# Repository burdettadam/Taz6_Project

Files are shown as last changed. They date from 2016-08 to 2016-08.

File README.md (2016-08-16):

# Taz6_Project
Analysis of building a cheap clone of the taz6 3d printer. 
# Goal
our goal is to analyse LulzBot TAZ 6 (https://www.lulzbot.com/store/printers/lulzbot-taz-6) open source 3d printer to create a cheap clone build by looking at alternative hardware and resulting trade offs.
all source files where taken from http://download.lulzbot.com/TAZ/6.0/. another place for source files can be found at http://devel.lulzbot.com/TAZ/Olive/
#to do
    -collect taz 6 source files-done
    -structure source files-done
    -created parts list with price total
#BOM
| Category | Part | Quantity |seller | Price |
|---|:---:|---:|---:|---:|
| Printed  |[Y Motor Mount v3.0](https://github.com/burdettadam/Taz6_Project/blob/master/production_parts/printed_parts/y_motor_mount/y_motor_mount_v3.0.stl),TAZ | 1 | | |
| |[Y mount table v~~2.5~~3.1](https://github.com/burdettadam/Taz6_Project/blob/master/production_parts/printed_parts/bed_mount_table/bed_mount_table_v3.1.stl), TAZ | 4 | | |
| |[Y Mount Chassis v~~2.5~~3.3A](https://github.com/burdettadam/Taz6_Project/blob/master/production_parts/printed_parts/bed_mount_chassis/bed_mount_chassis_v3.3_A.stl), TAZ | 4 | | |
| |[y idler mount v4.0](https://github.com/burdettadam/Taz6_Project/blob/master/production_parts/printed_parts/y_idler_mount/y_idler_mount_v4.0.stl), TAZ | 4 | | |
| |[Y belt mount v2.5](https://github.com/burdettadam/Taz6_Project/blob/master/production_parts/printed_parts/y_belt_mount/y_belt_mount_v0.75-x2.stl), TAZ | 1 | | |
| |[y corner left v2.4](https://github.com/burdettadam/Taz6_Project/blob/master/production_parts/printed_parts/y_corner_left/y_corner_left_v2.4.stl), TAZ | 4 | | |
| |[y corner right v2.4](https://github.com/burdettadam/Taz6_Project/blob/master/production_parts/printed_parts/y_corner_right/y_corner_right_v2.4.stl), TAZ | 4 | | |
| |[Bed corner ninjaflex-? v2.0](https://github.com/burdettadam/Taz6_Project/blob/master/production_parts/printed_parts/bed_corner_taz6/bed_corner_taz6_v2.stl), TAZ |  4 | | |
| |[bearing holder v1.0](https://github.com/burdettadam/Taz6_Project/blob/master/production_parts/printed_parts/bearing_holder/bearing_holder_v1.0.stl), TAZ |  ? | | |
| |[zmin switch mount v4.1](https://github.com/burdettadam/Taz6_Project/blob/master/production_parts/printed_parts/zmin_switch_mount/zmin_switch_mount_v4.1.stl) | 1 | | |
| |[Z-lower left](https://github.com/burdettadam/Taz6_Project/blob/master/production_parts/printed_parts/z_lower_left/z_lower_left_v2.5.stl) v2.5  | 2 | | |
| |[Z-lower right](https://github.com/burdettadam/Taz6_Project/blob/master/production_parts/printed_parts/z_lower_right/z_lower_right_v2.5.stl) v2.5  | 2 | | |
| |[Z Carriage Idler](https://github.com/burdettadam/Taz6_Project/blob/master/production_parts/printed_parts/z_carriage_idler/z_carriage_idler_v2.9.1.stl) | 1 | | |
| |[Z Carriage Motor](https://github.com/burdettadam/Taz6_Project/blob/master/production_parts/printed_parts/z_carriage_motor/z_carriage_motor_v2.10.stl) | 1 | | |
| |[Fan duct right v0.1](https://github.com/burdettadam/Taz6_Project/blob/master/production_parts/printed_parts/fan_duct_right/fan_duct_right_v0.7.4.1d.stl), TAZ |1 | | |
| |[Fan duct left v0.1](https://github.com/burdettadam/Taz6_Project/blob/master/production_parts/printed_parts/fan_duct_left/fan_duct_left_v0.7.4.1d.stl), TAZ |  1 | | |
| |[Single Bearing Holder for 12mm rod](https://github.com/burdettadam/Taz6_Project/blob/master/production_parts/printed_parts/12mm_single_bearing_holder/12mm_single_bearing_holder_v0.4.stl) v0.3 | 1 | | |
| |[Double Bearing Holder for 12mm rod](https://github.com/burdettadam/Taz6_Project/blob/master/production_parts/printed_parts/12mm_double_bearing_holder/12mm_double_bearing_holder_v0.7.stl) v0.3 | 1 | | |
| |[X-Carriage Guide](https://github.com/burdettadam/Taz6_Project/blob/master/production_parts/printed_parts/x_carriage_guide/x_carriage_guide_v2.stl) v2.0, TAZ | 1 | | |
| |[X-Carriage](https://github.com/burdettadam/Taz6_Project/blob/master/production_parts/printed_parts/x_carriage_taz6/x_carriage_taz6_v0.3.stl) v2.0, TAZ |1 | | |
| |[Wade extruder body for Hex nozzle](https://github.com/burdettadam/Taz6_Project/blob/master/production_parts/printed_parts/extruder_body_hex/extruder_body_hex_v1.4.1.stl) v1.0 |1 | | |
| |[Wiper mount](https://github.com/burdettadam/Taz6_Project/blob/master/production_parts/printed_parts/wiper_mount/wiper_mount_v1.1.stl) v2.0 |1 | | |
| |[extruder_latch_v2.1](https://github.com/burdettadam/Taz6_Project/blob/master/production_parts/printed_parts/extruder_latch/extruder_latch_v2.1.stl) | 1 | | |
| |[herringbone_small_gear](https://github.com/burdettadam/Taz6_Project/blob/master/production_parts/printed_parts/herringbone_small_gear/herringbone_small_gear-1.1-highres.stl) | 1 | | |
| |[herringbone_large_gear](https://github.com/burdettadam/Taz6_Project/blob/master/production_parts/printed_parts/herringbone_large_gear/herringbone_large_gear_v1.3.stl) | 1 | | |
| |[Wade Reloaded Bearing Washer](https://github.com/burdettadam/Taz6_Project/blob/master/production_parts/printed_parts/extruder_washer/extruder_washer_v3.0-x16.stl) | 1 | | |
| |[extruder_mount -?](https://github.com/burdettadam/Taz6_Project/blob/master/production_parts/printed_parts/extruder_mount_taz6/extruder_mount_taz6_v0.8.stl) | 1 | | |
| |[Wade Reloaded Idler Block](https://github.com/burdettadam/Taz6_Project/blob/master/production_parts/printed_parts/extruder_idler_block/extruder_idler_block_v1.4c.stl) v1.4, Taz | 1 | | |
| |[Feed Tube Spinner v2.5](https://github.com/burdettadam/Taz6_Project/blob/master/production_parts/printed_parts/feed_tube_spinner/feed_tube_spinner_v3.0.stl) | 1 | | |
| |~~Feed Tube Holder v2.5~~ -?  | 1 | | |
| |[tippy_feed_tube_holder_v0.6](https://github.com/burdettadam/Taz6_Project/blob/master/production_parts/printed_parts/tippy_feed_tube_holder/tippy_feed_tube_holder_v0.6.stl) -?damage stl?  | 1 | | |
| |[Spool Arm v2.0](https://github.com/burdettadam/Taz6_Project/blob/master/production_parts/printed_parts/spool_arm/spool_arm_v0.2-x2.stl), TAZ | 1 | | |
| |[heatsink fan duct](https://github.com/burdettadam/Taz6_Project/blob/master/production_parts/printed_parts/heatsink_fan/heatsink_fan_duct_v0.6.stl) | 1 | | |
| |[Z-Upper](https://github.com/burdettadam/Taz6_Project/blob/master/production_parts/printed_parts/z_upper/z_upper_v2.4.stl) v2.4 |  1 | | |
| |[LCD Bezel v1.1](https://github.com/burdettadam/Taz6_Project/blob/master/production_parts/printed_parts/lcd_bezel/lcd_bezel_v1.1.stl) |  4 | | |
| |[LCD Knob 0.2 design dent 2](https://github.com/burdettadam/Taz6_Project/blob/master/production_parts/printed_parts/lcd_knob/lcd_knob_0.2_design_dent_2.stl) |  1 | | |
| |[LCD spacer](https://github.com/burdettadam/Taz6_Project/blob/master/production_parts/printed_parts/lcd_spacer/lcd_spacer_v0.4.stl) |  4 | | |
| |[Sd Card Bezel v0.8](https://github.com/burdettadam/Taz6_Project/blob/master/production_parts/printed_parts/sd_card_bezel/sd_card_bezel_v0.8-x10.stl) |  4 | | |
| |[Electronics Case Mount v1.0](https://github.com/burdettadam/Taz6_Project/blob/master/production_parts/printed_parts/electronics_case_mount/electronics_case_mount_v2.0.stl) | 4 | | |
| |[Interconnect housing v0.1](https://github.com/burdettadam/Taz6_Project/blob/master/production_parts/printed_parts/interconnect_housing/interconnect_housing_v0.6.stl), TAZ |  1 | | |
| |[flexy washer v0.1](https://github.com/burdettadam/Taz6_Project/blob/master/production_parts/printed_parts/flexy_washer/flexy_washer_v0.1.stl), TAZ |  1 | | |
| |[flexy bed foot v0.1](https://github.com/burdettadam/Taz6_Project/blob/master/production_parts/printed_parts/flexy_bed_foot/flexy_bed_foot_v0.1.stl), TAZ |  1 | | |
| | | | | |
| Electronic | | | | |
| | | | | |
| Hardware | | | |
| | | | | |
| | | | [aliexpress](http://www.aliexpress.com/item/5-Hole-90-Degree-Joint-Board-Plate-Corner-Angle-Bracket-Connection-Joint-Strip-for-Aluminum-Profile/32669228356.html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,searchweb201602_1_10057_10056_10055_10049_10059_10058_10017_106_105_104_10060_103_10061_102_10062_10064,searchweb201603_1&btsid=93fedafa-1d70-452a-961e-7a9f04ef4315) | |
| Software | | | | |

#hardware lis cut paste from assemble instructions 
##Frame Sub Assy
4x- 500mm Aluminum Extrusion, M5 threaded one end  
4x- 510mm Aluminum Extrusion, ends not threaded  
41x- M5 T-Nut  
32x- M5x10 BHCS  
32x- M5 Washer, Black  
8x- Corner gussets  

##Bed Assy Sub
1x- Z switch mount (PP-GP0216)  
1x- Wiper Mount (PP-GP0231) and Wiper pad  
4x- Bearings Holder (PP-GP0233) (with bearings installed)  
4x- Bed corners (PP-GP0221)  
1x- Y belt mount (PP-GP0222)  
1x- Bed plate  
4x- Bed standoffs  
1x- Momentary switch and retention nut  
2x- SPDT switches  
1x- M3x16 FHCS  
30x- M3x8 BHCS  
4x- M2x10 SHCS  
1x- M3x10  
30x- M3 black washers  
4x- M2 washers  

##Y Axis Sub_Edit
16x- M5x10 BHCS  
16x- M5 Black Washer  
1x- M8x35 BHCS  
4x- M8 Washers  
2x- 608 bearings  
4x- M3x12 BHCS  
4x- M3 Black washers  
4x- M3x6 Set screws  
2x- 500mm aluminum extrusions  
16x- M5 T-Nut  
8x- M5x10 BHCS  

##Y axis end plate- Motor side
4x- M3x 10 BHCS  
4x- M3 Black Washer  
1x- Taz 6 Y Motor Mount (PP-GP0226)  
with 4x- M3 inserts installed  
1x- Y axis End plate  

##Idler assembly
1x- Idler mount (PP-GP0225) (with 4x M3 inserts)  
1x- M8 x40 BHCS  
4x- M8 Washer  
1x- M8 Nyloc Nut  
2x- 608 Bearing  

##Y Axis Idler end plate Assembly
4x- M3x 10 BHCS  
4x- M3 Black Washer  
1x- Taz 6 Y Axis Idler Assembly  
1x- Y axis End plate

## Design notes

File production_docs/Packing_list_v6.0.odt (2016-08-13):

Model: LulzBot TAZ 6 3D Printer

Serial Number: _______________________

Date Completed: _______________________

Completed by: _______________________

Items to include:

Printer and Cables:

- LulzBot TAZ 6 3D printer
- 1.83 meter (6ft) 18AWG North America Power Cord Cable
- 1.83 meter (6ft) 18AWG United Kingdom Power Cord Cable (If applicable)
- 1.83 meter (6ft) 18AWG Europe Power Cord Cable (If applicable)
- 1.83 meter (6ft) 18AWG Australia Power Cord Cable (If applicable)
- USB cord
- Filament guide tube with mounting clip
- Tool head assembly

Supplies:

- SD Card with source files
- Tool kit
- Sample material
- LulzBot sticker

Documentation:

- Unboxing guide
- Operating guide
- Test acceptance record
- Packing list
- User manual
- EC Declaration of Conformity
- Safety and warning sheet
- Modification warning

Final Print:

- Octopus printed by this LulzBot TAZ 3D Printer. Octopus_v18 by yeoldbrian is licensed under CC BY-SA 4.0

Packing List

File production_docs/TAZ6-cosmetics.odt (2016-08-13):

Purpose and Scope:

The purpose of this standard is to provide cosmetic requirements for printed components on TAZ 6. See 'Cosmetic Specification Requirements' document for definitions not included in this document. This does not include specifications for secondary operations such as inserts.

Components:

Z Upper

Z Lower

Z Carriage Idler

Z Carriage Motor

Z Gaskets

LCD Bezel:

Surface A as indicated should be free of any defects. All other surfaces not noted are defined as a 'D' surface.

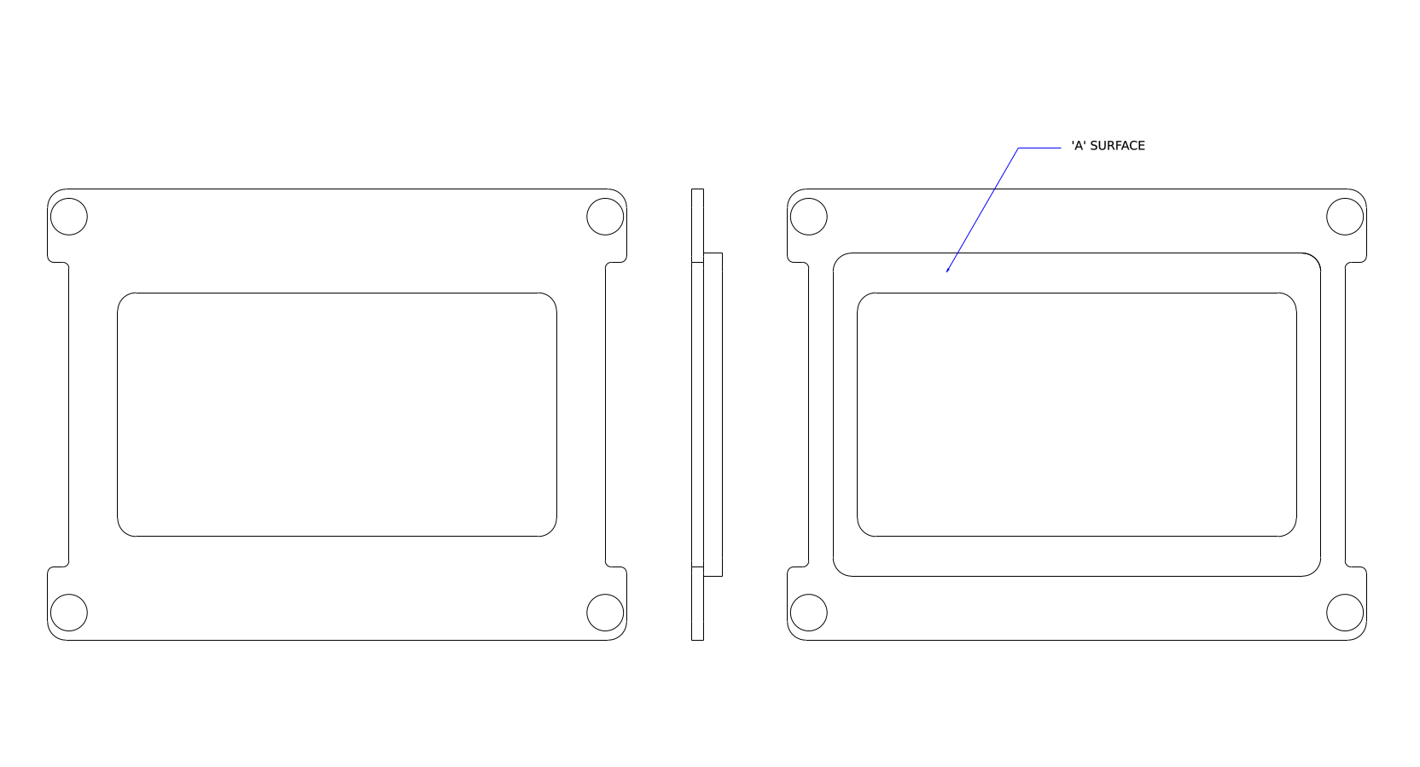
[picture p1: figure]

LCD Knob

SD Card

Lift: Lifting along an edge with a visible ridge.

(need sample picture)

Over squish: A solid first layer is present, the outside perimeter tapers out.

(need sample picture)

Resonance: See Ringing

(need sample picture)

Ringing: Wavy pattern after side face cutouts/holes.

(need sample picture)

Warp: Curling of the print at stressed locations of the print.

(need sample picture)

Wrinkling: Waving in the perimeter wall

(need sample picture)

II. Surface identifications and Classification of Surface Finish

“A” Surface – The top or front, most often viewed surface

“B” Surface – Generally the front edge and sides of a part. Not Viewed as often as an “A” surface but easily seen by user.

“C” Surface – Most often the back and bottom surface

“D” Surface - Internal surfaces. Normally D surfaces are not inspected for cosmetic attributes. Where necessary, D surfaces will be specified as an exception.

III. Standard Viewing Condition

A. Lighting Intensity

All quality decisions of cosmetic acceptability will be made under normal lighting conditions (80-120 footcandles) in white fluorescent light.

B. Viewing Angle

All viewing will take place with direct overhead lighting. Viewing angle is dependent on surface classification.

In every case, parts will be held such that the light is NOT REFLECTED directly to the viewer.

“A” Surface – Hold part 30º from the horizontal plane. Part is in direct line with your eyes.

ROTATE part 30º to the right and to the left about the vertical axis.

“B” Surface – Hold part 90º from the horizontal plane. Part is in direct line with your eyes. DO NOT rotate the part.

“C” Surface – Hold part 90º from the horizontal plane. Part is NOT in direct line with your eyes. Part is held 45º below the plane of your eyes. DO NOT rotate the part.

C. Viewing Distance

“A” Surface – 18 Inches

“B” Surface – 24 Inches

“C” Surface – 30 Inches

D. Inspection Interval (time)

Inspection interval is a function of surface area

SURFACE AREA | “A” Surfaces | Non - “A” Surfaces
≤ 4 in² ( | 2 sec | 1 sec
4-16 in² | 4 sec | 2 sec
16-64 in² | 6 sec | 3 sec
64-144 in² | 8 sec | 4 sec
> 144 in² | 10 sec | 5 sec

Cosmetic Specification Requirements TAZ 6

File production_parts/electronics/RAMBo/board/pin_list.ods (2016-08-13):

Port | Arduino Digital # | Function | RAMBo Function | Color | Function
PE0 | 0 | USART0_RX | USB/Serial Ext 3 |  | Serial
PE1 | 1 | USART0_TX | USB/Serial Ext 4 |  | MOSFET
PE4 | 2 | PWM2 | Fan-2 |  | Stepper
PE5 | 3 | PWM3 | Bed-Heat |  | I2C
PG5 | 4 | PWM4 | PS-On/PWM Ext 6 |  | Ext2
PE3 | 5 | PWM5 | PWM Ext 5 |  | Analog In
PH3 | 6 | PWM6 | Fan-1 |  | SPI
PH4 | 7 | PWM7 | Heat-1 |  | PWM
PH5 | 8 | PWM8 | Fan-0 |  | Stepper Ext
PH6 | 9 | PWM9 | Heat-0 |  | Endstop
PB4 | 10 | PWM10 | Z-Min |  | Endstop/Stepper Ext
PB5 | 11 | PWM11 | Y-Min
PB6 | 12 | PWM12 | X-Min
PB7 | 13 | PWM13 | LED/PWM Ext 3
PJ1 | 14 | USART3_TX | Serial Ext 10
PJ0 | 15 | USART3_RX | Serial Ext 9
PH1 | 16 | USART2_TX | Serial Ext 8
PH0 | 17 | USART2_RX | Serial Ext 7
PD3 | 18 | USART1_TX | Serial Ext 6
PD2 | 19 | USART1_RX | Serial Ext 5
PD1 | 20 | I2C_SDA | I2C Ext 3
PD0 | 21 | I2C_SCL | I2C Ext 4
PA0 | 22 | D22 | MX1-3
PA1 | 23 | D23 | Y-Max/MX3-3
PA2 | 24 | D24 | X-Max/MX2-3
PA3 | 25 | D25 | E1-En
PA4 | 26 | D26 | E0-En
PA5 | 27 | D27 | Z-En
PA6 | 28 | D28 | Y-En
PA7 | 29 | D29 | X-En
PC7 | 30 | D30 | Z-Max/MX2-4
PC6 | 31 | D31 | MX3-4
PC5 | 32 | D32 | MX1-4
PC4 | 33 | D33 | E1-Step
PC3 | 34 | D34 | E0-Step
PC2 | 35 | D35 | Z-Step
PC1 | 36 | D36 | Y-Step
PC0 | 37 | D37 | X-Step
PD7 | 38 | D38 | DigiPot-SS
PG2 | 39 | D39 | Y-MS2
PG1 | 40 | D40 | X-MS1
PG0 | 41 | D41 | X-MS2
PL7 | 42 | D42 | E1-Dir
PL6 | 43 | D43 | E0-Dir
PL5 | 44 | D44 | MX1-5
PL4 | 45 | D45 | MX3-5
PL3 | 46 | D46 | MX2-5
PL2 | 47 | D47 | Z-Dir
PL1 | 48 | D48 | X-Dir
PL0 | 49 | D49 | Y-Dir
PB3 | 50 | SPI_MISO | SPI Ext 3
PB2 | 51 | SPI_MOSI | SPI Ext 4
PB1 | 52 | SPI_SCK | SPI Ext 5
PB0 | 53 | SPI_SS | SPI Ext 6
PF0 | 54 | A0 | T0
PF1 | 55 | A1 | T1
PF2 | 56 | A2 | T2
PF3 | 57 | A3 | Analog Ext 8
PF4 | 58 | A4 | Analog Ext 6
PF5 | 59 | A5 | Analog Ext 4
PF6 | 60 | A6 | Analog Ext 3
PF7 | 61 | A7 | T3/Analog Ext 5
PK0 | 62 | A8 | Analog Ext 7
PK1 | 63 | A9 | E1-MS1
PK2 | 64 | A10 | E1-MS2
PK3 | 65 | A11 | E0-MS1
PK4 | 66 | A12 | E0-MS2
PK5 | 67 | A13 | Z-MS2
PK6 | 68 | A14 | Z-MS1
PK7 | 69 | A15 | Y-MS1
PG4 | 70 | D70 | Ext2 5
PG3 | 71 | D71 | Ext2 7
PJ2 | 72 | D72 | Ext2 9
PJ3 | 73 | D73 | Ext2 11
PJ7 | 74 | D74 | Ext2 13
PJ4 | 75 | D75 | Ext2 15
PJ5 | 76 | D76 | Ext2 17
PJ6 | 77 | D77 | Ext2 19
PE2 | 78 | D78 | Ext2 20
PE6 | 79 | D79 | Ext2 18
PE7 | 80 | D80 | Ext2 16
PD4 | 81 | D81 | Ext2 14
PD5 | 82 | D82 | Ext2 12
PD6 | 83 | D83 | Ext2 10
PH2 | 84 | D84 | Ext2 8
PH7 | 85 | D85 | Ext2 6

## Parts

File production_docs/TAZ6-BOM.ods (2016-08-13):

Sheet: Olive
Category | AO Part # | Description | Manufacturer | Manufacturer Part Number | Distributor | Distributor SKU | Qty Per | UOM | Price Per Unit | Price Total | Qty to Order | PO | Date | ETA | R&D notes
OK to order |  | BOLD MEANS ORDERED FOR OLIVE ALSO |  |  |  |  |  |  |  | $958.18 | 3,050
Sheet metal out for quote | received | Kim please purchase
Printed – Approved |  | Buy now, Long lead times
Printed – Not approved |  | Order now!
Not confirmed – Don't order yet
 |  | NEW part number created
already ordered
questionable |  | Toni will handle
Printed | PP-GP0226 | Y Motor Mount v3.0, TAZ |  |  |  |  | 1 | ea | $5.17 | $5.17 | 3,050
Printed | PP-GP0225 | Y Bearing Mount v3.0, TAZ |  |  |  |  | 1 | ea | $0.97 | $0.97 | 3,050
Printed | PP-GP0224 | Y mount table v2.5, TAZ |  |  |  |  | 4 | ea | $0.73 | $2.92 | 12,200
Printed | PP-GP0223 | Y Mount Chassis v2.5, TAZ |  |  |  |  | 4 | ea | $0.73 | $2.92 | 12,200 |  |  |  | resize for M5 x 12
Printed | PP-GP0222 | Y belt mount v2.5, TAZ |  |  |  |  | 1 | ea | $2.46 | $2.46 | 3,050
Printed | PP-GP0221 | Bed corner ninjaflex v1.0, TAZ |  |  |  |  | 4 | ea | $0.29 | $1.16 | 12,200
Printed | PP-GP0216 | Switch mount |  |  |  | PP-GP0216 | 1 | pcs | $2.00 | $2.00 | 3,050
Printed | PP-GP0215 | Z-lower v0.1, Mangrove left |  |  |  | PP-GP0215 | 2 | pcs | $6.00 | $12.00 | 6,100 |  |  |  | Add 2mm material for m3
Printed | PP-GP0214 | Z Carriage Idler |  |  |  | PP-GP0214 | 1 |  | $6.00 | $6.00 | 3,050 |  |  |  | Name will likely change
Printed | PP-GP0213 | Z Carriage Motor |  |  |  | PP-GP0213 | 1 |  | $6.00 | $6.00 | 3,050 |  |  |  | Name will likely change
Printed | PP-GP0212 | Fan duct right v0.1, TAZ |  |  |  |  | 1 | pcs | $1.70 | $1.70 | 3,050
Printed | PP-GP0211 | Fan duct left v0.1, TAZ |  |  |  |  | 1 | pcs | $1.70 | $1.70 | 3,050
Printed | PP-GP0210 | Single Bearing Holder for 12mm rod v0.3 |  |  |  |  | 1 | ea | $1.17 | $1.17 | 3,050
Printed | PP-GP0209 | Double Bearing Holder for 12mm rod v0.3 |  |  |  |  | 1 | ea | $2.89 | $2.89 | 3,050
Printed | PP-GP0208 | Dual fan hextruder mount v0.5 |  |  |  |  | 1 | ea | $6.51 | $6.51 | 3,050
Printed | PP-GP0207 | X-Carriage Guidev2.0, TAZ |  |  |  |  | 1 | ea | $0.76 | $0.76 | 3,050
Printed | PP-GP0206 | X-Carriage v2.0, TAZ |  |  |  |  | 1 | ea | $6.00 | $6.00 | 3,050
Printed | PP-GP0186 | Wade extruder body for Hex nozzle v1.0 |  |  |  |  | 1 | ea | $4.01 | $4.01 | 3,050
Printed | PP-GP0231 | Wiper mount v2.0 |  |  |  |  | 1 | ea | $1.00 | $1.00 | 3,050 |  |  |  | needs to be modified so m3x8 doesnt poke through bottom of plate
Printed | PP-GP0091 | extruder_latch_v2.1 |  |  |  |  | 1 | ea | $0.26 | $0.26 | 3,050
Printed | PP-GP0062 | herringbone_small_gear |  |  |  |  | 1 | ea | $0.34 | $0.34 | 3,050
Printed | PP-GP0061 | herringbone_large_gear |  |  |  |  | 1 | ea | $2.43 | $2.43 | 3,050
Printed | PP-GP0060 | Wade Reloaded Bearing Washer |  |  |  |  | 1 | ea | $0.02 | $0.02 | 3,050
Printed | PP-GP0059 | Wade Reloaded Idler Block v1.4, Taz & Mini |  |  |  |  | 1 | ea | $0.90 | $0.90 | 3,050
Printed | PP-GP0219 | Feed Tube Spinner v2.5 |  |  |  | PP-GP0219 | 1 | ea | $0.53 | $0.53 | 3,050 |  |  |  | widen hole
Printed | PP-GP0218 | Feed Tube Holder v2.5 |  |  |  | PP-GP0218 | 1 | ea | $0.66 | $0.66 | 3,050 |  |  |  | round corners
Printed | PP-GP0217 | Spool Arm v2.0, TAZ |  |  |  | PP-GP0217 | 1 | ea | $2.01 | $2.01 | 3,050 |  |  |  | should be good to go
Printed |  | heatsink fan duct |  |  |  |  | 1 | pcs | $1.25 | $1.25 | 3,050 |  |  |  | duplicate, part number at bottom of doc
Printed |  | Z-Upper v0.1 |  |  |  |  | 2 | pcs | $5.00 | $10.00 | 6,100 |  |  |  | duplicate, part number at bottom of doc
Printed | PP-GP0089 | LCD_spacer |  |  |  |  | 4 | ea | $0.10 | $0.40 | 12,200
Printed | PP-GP0154 | Electronics Case Mount v1.0 |  |  |  |  | 4 | ea | $0.24 | $0.96 | 12,200
Printed | PP-GP0220 | Interconnect housing v0.1, TAZ |  |  |  |  | 1 | pcs | $5.00 | $5.00 | 3,050
Accessories | SH-PG0031 | Anti-Static Control Products 2X3 STATIC SHLD BAG W/ZIP TOP | Uline | S-6509 | Uline | S-6509 | 1 | ea | $0.13 | $0.13 | 3,050 | PO11679 | 01/25/16 | 02/29/16 | Received OLIVE BOM Ordered. KG
Accessories | DC-LB0007 | Label, Top of Box |  |  |  |  | 1 | ea | $0.24 | $0.24 | 3,050 |  |  |  | Pending Ben and Steven – looks like these will be printed on the box
Accessories | DC-LB0024 | Label, Bottom of Box |  |  |  |  | 1 | ea | $0.24 | $0.24 | 3,050 |  |  |  | Pending Ben and Steven – looks like these will be printed on the box
Accessories | SH-PG0069 | 3M 8898 Economy Strapping Tape - 1⁄2" x 60 yards |  |  | Uline | S-16075 | 700 | mm | $0.00 | $0.09 | 2,135,000 | PO12719 | 03/29/16 | 04/04/16 | 7005 ft = 2400 yds = 48 rolls KG Have new packaging vendor quote this out.TS
Accessories | SH-PG0072 | 3M 8898 Economy Strapping Tape - 2" x 60 yards |  |  | Uline | S-16076 | 600 | mm | $0.00 | $0.50 | 1,830,000 | PO12719 | 03/29/16 | 04/04/16 | 6004 ft = 2002 yds = 36 rolls KG
Accessories | DC-LB0023 | Circle Inventory Control Labels - "QC Passed" |  |  | Uline | S-13118 | 1 | ea | $0.04 | $0.04 | 3,050 |  |  |  | removed per Mickey's request
Accessories | DC-LB0021 | Circle Inventory Control Labels - "Inspected by ____" |  |  | Uline | S-13119 | 1 | ea | $0.04 | $0.04 | 3,050 |  |  |  | removed per Mickey's request
Accessories | SH-BX0051 | TAZ 6 Box White: 34-1/2 x 11-3/16 x 25 RSC, 51ECT, Double Wall, White, 2 Colors, Glue Joint | Preferred Packaging Products |  | Preferred Packaging Products |  | 1 | ea | $6.20 | $6.20 | 3,050 | PO12299 | 03/07/16 | See notes | Deliveries of ~ 150 units per week to be delivered on Fridays for the following week's production. Initial delivery TBD. Deliveries can be increased or decreased upon demand and we have until Sept. 1, 2016 to pull in the total of the units.
Accessories | SH-BX0052 | TAZ 6 Bed Insert: 19-5/8 x 17-1/8 Die Cut, 44 ECT, C Flute, Kraft, Plain | Preferred Packaging Products |  | Preferred Packaging Products |  | 1 | ea | $0.58 | $0.58 | 3,050 | PO12299 | 03/07/16 | See notes | Deliveries of ~ 150 units per week to be delivered on Fridays for the following week's production. Initial delivery TBD. Deliveries can be increased or decreased upon demand and we have until Sept. 1, 2016 to pull in the total of the units.
Accessories | SH-BX0053 | TAZ 6 Scored Pad: 10-3/8 x 28-3/4 Scored Pad, 44 ECT, C Flute, Kraft, Plain | Preferred Packaging Products |  | Preferred Packaging Products |  | 1 | ea | $1.77 | $1.77 | 3,050 | PO12299 | 03/07/16 | See notes | Deliveries of ~ 150 units per week to be delivered on Fridays for the following week's production. Initial delivery TBD. Deliveries can be increased or decreased upon demand and we have until Sept. 1, 2016 to pull in the total of the units.
Accessories | SH-BX0054 | TAZ 6 U-Pad: 25 x 19-7/16 Scored Pad, 51 ECT, Double Wall, Kraft, Plain | Preferred Packaging Products |  | Preferred Packaging Products |  | 1 | ea | $0.67 | $0.67 | 3,050 | PO12299 | 03/07/16 | See notes | Deliveries of ~ 150 units per week to be delivered on Fridays for the following week's production. Initial delivery TBD. Deliveries can be increased or decreased upon demand and we have until Sept. 1, 2016 to pull in the total of the units.
Accessories | SH-BX0025 | TAZ 6 Tool Head and Accessory Box: 9-1/2 x 7 x 3-7/8 Die Cut, 32 ECT, B Flute, Kraft, Plain | Preferred Packaging Products |  | Preferred Packaging Products |  | 2 | ea | $1.68 | $3.36 | 6,100 | PO12299 | 03/07/16 | See notes | 1 Box is for the tool head with custom foam insert and the 2ns is for accessories. TS Deliveries of ~ 150 units per week to be delivered on Fridays for the following week's production. Initial delivery TBD. Deliveries can be increased or decreased upon demand and we have until Sept. 1, 2016 to pull in the total of the units.
Accessories | SH-MS0056 | TAZ 6 Hand Hole Liners: Allenfield 350010 Clean Lift Handle Inserts | Preferred Packaging Products |  | Preferred Packaging Products |  | 2 | ea | $0.40 | $0.80 | 6,100 | PO12299 | 03/07/16 | See notes | Deliveries of ~ 150 units per week to be delivered on Fridays for the following week's production. Initial delivery TBD. Deliveries can be increased or decreased upon demand and we have until Sept. 1, 2016 to pull in the total of the units.
Accessories | SH-PG0122 | TAZ 6 Foam: End Cap and Corner Set, 1.5 lb. Density Expanded Polyethylene Foam, Black | Preferred Packaging Products |  | Preferred Packaging Products |  | 1 | ea | $19.33 | $19.33 | 3,050 | PO12300 | 03/08/16 | See notes | Deliveries of ~ 150 units per week to be delivered on Fridays for the following week's production. Initial delivery TBD. Deliveries can be increased or decreased upon demand and we have until Sept. 1, 2016 to pull in the total of the units.
Accessories | SH-PG0123 | TAZ 6: Tool Head Foam Insert: 1.2 lb. Density Extruded Polyethylene Foam, Gray | Preferred Packaging Products |  | Preferred Packaging Products |  | 1 | ea | $2.18 | $2.18 | 3,050 | PO12301 | 03/09/16 | See notes | Deliveries of ~ 150 units per week to be delivered on Fridays for the following week's production. Initial delivery TBD. Deliveries can be increased or decreased upon demand and we have until Sept. 1, 2016 to pull in the total of the units.
Accessories | HD-MS0348 | ESD Foam 40mm x 20mm x 10mm – Extruder Pin Protector | PaqSource |  | PaqSource |  | 1 | ea | $0.07 | $0.07 | 3,050 | PO11021 | See notes |  | We do not need to order these since Paq Source provided 10,000 units und PO11021 for free do to an inconvenience.
Accessories | SH-BX0032 | 30x24x13 CUSTOM BOX | Shippers' Supply Custom Pack |  | Shippers' Supply Custom Pack |  | 1 | ea | -$4.14 | -$4.14 | 3,050 |  |  |  | Please see me on this, vetting new packaging vendor. TS
Accessories | SH-BX0025 | 10x8x2-1/2 32 Ect B Brown Roll End Tuck Mailer, Custom Box | Shippers' Supply Custom Pack |  | Shippers' Supply Custom Pack |  | 1 | ea | -$0.65 | $0.41 | 3,050 |  |  |  | Please see me on this, vetting new packaging vendor. TS
Accessories | SH-PA0040 | Fabricated Foam Insert: 2 End Caps, Tray w/Plastic Corrugated & Plain Pad, v5 | Shippers' Supply Custom Pack |  | Shippers' Supply Custom Pack |  | 1 | ea | -$37.95 | -$37.95 | 3,050 |  |  |  | Please see me on this, vetting new packaging vendor. TS
Accessories | SH-PG | White Security Kraft Tape | Preferred Packaging Products |  | Preferred Packaging Products |  |  |  |  |  |  |  |  |  | (3/31 We are wating on Art for this. TS)
Accessories | SH-PG0056 | Kraft packing tape, tan, 3x450', gummed | Shippers' Supply Custom Pack |  | Shippers' Supply Custom Pack |  | 4267 | mm |  |  | 13,014,350 |  |  |  | Please see me on this, vetting new packaging vendor. TS
Accessories | SH-PA0025 | CUSTOM PAD 4-1/2X9-38 | Shippers' Supply Custom Pack |  | Shippers' Supply Custom Pack |  | 1 | ea | -$0.16 | -$0.16 | 3,050 |  |  |  | Please see me on this, vetting new packaging vendor. TS
Consumable | TL-CS0115 | 5 Gallon DYKEM[REG] Metal Can Acetone | Fastenal | 607086 | Fastenal | 607086 | 0.00027 | 5gal bucket | $93.26 | $0.02 | 0 | PO06975 | See notes | See Note | Standing PO06975 – we need to just call this in as needed.TS
Consumable | TL-CS0040 | Extreme-Temperature Pipe Sealant & Threadlocker, 4 oz bottle, blue | Threadlocker | 7604A55 | McMaster-Carr | 7604A55 | 0.5 | g | $0.07 | $0.03 | 1,525 |  | See notes | See Note | We order this as needed.TS
Consumable | TL-CS0169 | Loctite® Threadlocker 220, 0.34 oz. Bottle | Threadlocker | 1810A315 | McMaster-Carr | 1810A315 | 0.5 | g | $0.07 | $0.03 |  |  | See notes | See Note | We order this as needed due to expiration dates vs. consumption, etc. TS Per Mickey this is replacing part number TL-CS0140 (Which I did not see on this BOM prior, might have gotten updated by R&D before I was aware.TS
Consumable | RM-AB0103 | Black ABS 3mm Filament, 5lb Reel, Esun | Esun | RM-AB0103 | Esun | RM-AB0103 | 4.133 | g |  |  |  |  |  | See Note | Pulling from the Cluster
Consumable | RM-MS0035 | nGen Amphora (colorFabb) 2.85 mm filament, .75kg Reel, AM3300 Polymer, LulzBot Green | colorFabb |  | colorFabb |  | 4.133 | g | $0.00 |  |  | PO12115 | 02/25/16 | 03/04/16 | No costing on these samples – we are getting them for Free! TS
Documentation | DC-MN0015 | Lulzbot-Taz 6.0 User Manual | Lightning Source |  |  |  | 1 | ea | $4.75 | $4.75 | 3,050 | PO12729 | 03/29/16 | 03/30/16 | First 400 ordered at premium for quick delivery NEW part number
Documentation | DC-MS0049 | Test/Acceptance record TAZ 6.0 | 2 SIDED |  |  |  | 1 | ea | $0.48 | $0.48 | 3,050 | PO12745 | 04/01/16 | 04/03/16
Documentation |  | Quality checklist, TAZ 6.0 |  |  |  |  | 1 | ea | $0.76 | $0.76 | 3,050
Documentation | DC-MS0050 | Packing List, TAZ 6.0 |  |  |  |  | 1 | ea | $0.24 | $0.24 | 3,050 | PO12745 | 04/01/16 | 04/03/16
Documentation | DC-MN0016 | Operating Guide, TAZ 6.0 |  |  |  |  | 1 | ea | $1.62 | $1.62 | 3,050 | PO12745 | 04/01/16 | 04/03/16 | NEW part number
Documentation | DC-MS0051 | Declaration of Conformity, TAZ 6.0 |  |  |  |  | 1 | ea | $0.11 | $0.11 | 3,050 | PO12745 | 04/01/16 | 04/03/16 | NEW part number
Documentation | DC-LB0063 | Modification Warning Insert Modification 2.75 x 8.5 on 100 lb. Astrobright Lift Off Lemon Very Bright |  |  |  |  | 1 | ea | $0.07 | $0.07 | 3,050 | PO12745 | 04/01/16 | 04/03/16
Documentation | DC-MN0017 | Unboxing Guide TAZ 6 |  |  |  |  | 1 | ea |  |  |  |  |  |  | NEW part number
Documentation | DC-MS0052 | Safety Warnings sheet, TAZ 6.0 |  |  |  |  | 1 | ea
Electronic | PC-CN0062 | Female 8 pin Molex Connector Housing | Molex | 50-57-9408 | TTI | 538-50-57-9408 | 1 | pcs | $0.12 | $0.12 | 3,050 | PO11064 | 12/04/15 | 02/22/16 | Ordered for Olive.KG
Electronic | PC-CN0061 | Male 8 pin Molex Connector Housing | Molex | 70107-0007 | TTI | 538-70107-0007 | 1 | pcs | $0.37 | $0.37 | 3,050 | PO11064 | 12/04/15 | 02/22/16 | Ordered for Olive.KG
Electronic | PC-CN0059 | Male 10 pin Molex Connector Housing | Molex | 70107-0009 | TTI | 538-70107-0009 | 1 | pcs | $0.40 | $0.40 | 3,050 | PO11064 | 12/04/15 | 02/22/16 | Ordered for Olive.KG
Electronic | PC-CN0057 | Male 16 pin Molex Connector Housing | Molex | 70107-0015 | SAGER | 538-70107-0015 | 1 | pcs | $0.63 | $0.63 | 3,050 | PO11065 | 12/04/15 | 12/11/15 | Ordered for Olive.KG
Electronic | PC-CN0055 | Headers & Wire Housings Male 20Ckt | Molex | 70107-0019 | SAGER | 538-70107-0019 | 1 | pcs | $0.79 | $0.79 | 3,050 | PO11065 | 12/04/15 | 12/11/15 | Ordered for Olive.KG
Electronic | PC-CN0053 | Headers & Wire Housings HSG 12P W/O Ears Single Row | Molex | 70107-0011 | SAGER | 538-70107-0011 | 1 | pcs | $0.62 | $0.62 | 3,050 | PO11065 | 12/04/15 | 12/11/15 | Ordered for Olive.KG
Electronic | PC-CN0001 | Molex-Conn Housing 2POS .100 W/Latch | Molex | 50579402 | SAGER | WM2900-ND | 8 | ea | $0.05 | $0.42 | 24,400 | PO11031 / PO11661 | 12/03/15 | See notes | Ordered additional units for Olive.KG
Electronic | PC-AS0019 | Full Graphic Smart LCD Controller, gLCD Kit | RepRapDiscount |  | RepRapDiscount |  | 1 | ea | $28.00 | $28.00 | 3,050 | PO10917 | 12/03/15 | See notes | Received Ordered for Olive. KG
Accessories | EL-MS0119 | SD Card from GLCD Kit | These come with PC-AS0019 |  | These come with PC-AS0019 |  | 1 | ea | $0.00 |  | 3,050 | PO10917 | 12/08/15 | 12/15/15 | Received Ordered for Olive. KG
Electronic | PC-BD0045 | RAMBO Electronics v1.3L | UltiMachine |  |  |  | 1 | ea | $78.00 | $78.00 | 3,050 | PO10930 | 12/03/15 | See notes | Received 1050 & 30 next delivery 3/11/16 KG Order for Olive.KG
Electronic | HD-TB0032 | Flexible Polyolefin Heat Shrink Tubing 1/8" ID Before, 1/16" ID After, 100' L, Black | EDC | 84-01250 | McMaster-Carr | 7856K33 | 40 | mm | $0.00 | $0.06 | 120 | PO11684 | 02/01/16 | 03/07/16 | OLIVE KG 5/100' (400ft) for OliveEDC quoted 100' = $ 18.68 /100' Allcable sending sample for alternatel quote costing and lead time. TS
Electronic | EL-WR0120 | 24AWG Stranded – Purple | Allcable | HU1569247VT | Allcable | HU1569247VT | 2810 | mm | $0.00 | $0.21 | 8,570,500 | PO11346 | 01/08/16 | 02/05/16 | X-max, 2x 185 | 28,395' for NUTMEG and OLIVE
Electronic | EL-WR0119 | 24AWG Stranded – Green | Allcable | HU1569247GN | Allcable | HU1569247GN | 3040 | mm | $0.00 | $0.23 | 9,272,000 | PO11346 | 01/08/16 | 02/05/16 | 5v fan | 31,174' for NUTMEG AND OLIVE
Electronic | EL-WR0111 | 24AWG Stranded – Blue | Allcable | HU1569247BE | Allcable | HU1569247BE | 3300 | mm | $0.00 | $0.25 | 10,065,000 | PO11346 / PO11664 | 01/22/16 | 2/118/16 | fan0 main – See PO11664 for increased quantity. TS | 30,922 ' for NUTMEG AND OLIVE
Electronic | EL-WR0109 | 24AWG Stranded – Yellow | Allcable | HU1569247YW | Allcable | HU1569247YW | 3240 | mm | $0.00 | $2.44 | 9,882,000 | PO11346 | 01/08/16 | 02/05/16 | 5v fan | 38,652' FOR NUTMEG AND OLIVE
Electronic | EL-WR0135 | WIRE MTW 16AWG PPL 500ft REEL 600V 19-STRAND BARE COPPER – Purple | Allcable / AutomationDirect | MTW16PL25 | Allcable / AutomationDirect | MTW16VT / MTW16PL25 | 840 | mm | $0.00 | $0.16 | 2,562,000 | PO11346 | 01/07/16 | 02/05/16 | Delivered KG ORDERED FOR OLIVE KG from allcable 5' ea, 142 ft for Nutmeg, 14,500' needed for OLIVE
Electronic | EL-WR0107 | 24AWG Stranded – White | Allcable | HU1569247WE | Allcable | HU1569247WE | 1990 | mm | $0.00 | $0.15 | 6,069,500 | PO11346 / PO11664 | 01/22/16 | 02/18/16 | fan0 main See PO11664 for increased Quantities. TS | 15,259' FOR NUTMEG AND OLIVE
Electronic | EL-WR0105 | 24AWG Stranded – Black | Allcable | HU1569247BK | Allcable | HU1569247BK | 2170 | mm | $0.00 | $0.16 | 6,618,500 | PO11346 / PO11664 | 01/22/16 | 02/18/16 | See PO11664 for increased Quantities. TS | 20,665 FOR NUTMEG AND OLIVE
Electronic | EL-WR0104 | 24AWG Stranded – Orange | Allcable | HU1569247OE | Allcable | HU1569247OE | 4540 | mm | $0.00 | $0.34 | 13,847,000 | PO11346 / PO11664 | 01/22/16 | 02/18/16 | 1020 x 2 leads See PO11664 for increased Quantities. TS | 35,267' FOR NUTMEG AND OLIVE
Electronic | EL-WR0103 | 24AWG Stranded – Red | Allcable | HU1569247RD | Allcable | HU1569247RD | 4390 | mm | $0.00 | $0.33 | 13,389,500 | PO11346 | 01/08/16 | 02/05/16 |  | 43,300' FOR NUTMEG AND OLIVE
Electronic | EL-WR0099 | Shielded 4Cond 22AWG | Allcable | C0762A.41.10 | Allcable | C0762A.41.10 | 3825 | mm | $0.00 | $3.87 | 11,666,250 | PO12258 | 02/26/16 | 03/17/16 | Received partial, balance due 3/17 KG39,000 ft for Olive | Eric double checked the length by summing the lengths in the drawings
Electronic | EL-SW0030 | Momentary Metal Flat Flush Mount Push Button Switch | Parts Express | 060-660 | Parts Express | 66-2436 | 1 | ea | $3.44 | $3.44 | 3,050 | PO11059 /PO11089 | 12/04/15 | 02/05/16 | 400 pc Balance due first of April, Received 2650 pcs KG 3050 pcs ordered for Olive Online.KG 1000 pc balance on 1/25 shipped 600, balance ETC April 1st week KG – WE ARE TRYING TO HAVE SAGER HELP US PURCHASE THIS SWITCH FROM PARTS EXPRESS, ALSO TRYING TO CONTACT PARTS Eric K confirmed this part is correct and needed for Nutmeg build. PO to EXPRESS DIRECTLY TO SECURE STOCK FOR OLIVE. Site showing long lead times on quantities.
Electronic | EL-SW0021 | Switch SIM Roll SPDT 3A 125V | Omron | SG-3GL13PT | TTI | SW768-ND | 5 | ea | $0.59 | $2.96 | 15,250 | PO10843, 10919 | 12/03/15 | 02/15/16 | RECEIVED TTI has 2100 units in stock – Nutmeg PO10843, 5000 4 weeks, will expedite remaining 20650 for olive PO10919*
Electronic | EL-SW0023 | SWITCH ROCKER DPST 20A 250V, illuminated red | Heilind / Cyclops | R5BBLKREDFF2 | Heilind / Cyclops | R5BBLKREDFF2 | 1 | ea | $1.47 | $1.47 | 3,050 | PO08916, 11043 | 12/03/15 | 02/05/16 | RECEIVED Cyclops special buy PO08916 will support Nutmeg. Heilind PO11043 is Olive.
Electronic | EL-MT0029 | NEMA 17 Stepper Motor, Moons' - NOT INCLUDING wire harness - As per attached Drawing. | Moons | MS17HD6P4150MS17HD6P4150-01-B | Moons | MS17HD6P4150-01-B | 5 | ea | $8.30 | $41.50 | 15,250 | PO11681 | 01/25/16 | 03/08/16 | The first 1500 units might have to ship via Air, remaining units will come FOB Chicago as needed to meet production. TS
Electronic | EL-MS0351 | JST – CONN TERM CRIMP PH 24-30AWG | JST Sales America, Inc. | SPH-002T-P0.5S | Digi-Key /Future Electronics | 455-1127-1-ND | 20 | pcs | $0.01 | $0.25 | 61,000 | PO11082, PO11270 | 12/08/15 | 12/10/15 | RECEIVED Nutmeg Digikey PO11082, 8000 reel. Ordered from Future for OLIVE KG
Electronic | EL-MS0251 | CONN HOUSING 16POS .100 DUAL | Molex | 22552161 | TTI | 22552161 | 2 | ea | $0.53 | $1.06 | 6,100 | PO11064 | 12/04/15 | 12/10/15 | Received 50 /50 Ordered for Olive.KG
Electronic | EL-MS0205 | Molex-CONN TERM MALE 22-24AWG TIN - Reels of 20K | Molex | 16-02-0107 | TTI | 16-02-0107 | 69 | ea | $0.02 | $1.28 | 210,450 | PO11064 | 12/04/15 | 12/10/15 | Received 20,000 reels Ordered for Olive.KG
Electronic | EL-MS0142 | Conn Recept Faston 22-26AWG .110 - Reel of 3K | Molex | 7-520365-2 | TTI | 7-520365-2 | 10 | ea | $0.08 | $0.76 | 30,500 | PO11064 | 12/04/15 | 12/10/15 | Received 3000 reel Ordered for Olive.KG
Electronic | EL-MS0141 | Term Ring Non Ins 26-22AWG #4 Order Bulk Only | Panduit | P22-4R-M | TTI | P22-4R-M | 10 | ea | $0.06 | $0.59 | 30,500 | PO10936, 11088 | 12/03/15 | 02/22/16 | RECEIVED TTI has stock available, no Ltime Check lead time with vendor and order accordingly. TS Delivering on 12/10/15 & 2/5/16.KG Ordered PO11088 for Olive.KG
Electronic | EL-MS0139 | Tubing Corrugated Loom 3/8" ID, Black | Panduit / Fastenal | 0708162 | Electronics Distributors Corp. | 3/8" Black Split Loom, Box 1900 | 1350 | mm | $0.00 | $0.00 | 4,117,500 | PO11684 | 02/01/16 | 03/07/16 | 5,700' will deliver ~ 3/23 received 9,500 of 14,000' ordered for OLIVE KG
Electronic | EL-MS0073 | Tubing Corrugated Loom .25", Black | Panduit / Fastenal | 0708161 | EDC – Electronics Distributors Corporation | 1/4" Black Split Loom, Box 3200' | 1385 | mm | $0.00 | $0.00 | 4,224,250 | PO11684 | 02/01/16 | 03/07/16 | 15,200' OLIVE
Electronic | EL-MS0062 | MOLEX-CONN HOUSING 4POS .100 W/LATCH | Molex | 50579404 | Sager | 50579404 | 6 | ea | $0.05 | $0.31 | 18,300 | PO11065 | 12/08/15 | 02/05/16 | Ordered for Olive KG
Electronic | EL-MS0061 | Molex-CONN HOUSING MALE 4POS .100 | Molex | 701070003 | Sager | 701070003 | 1 | ea | $0.12 | $0.12 | 3,050 | PO11065 | 12/08/15 | 02/05/16 | Ordered for Olive KG
Electronic | EL-MS0059 | CONN TERM FEMALE 22-24AWG TIN | Molex Inc. | 16-02-0086 | TTI | WM2510TR-ND | 145 | ea | $0.01 | $2.10 | 442,250 | PO11064 | 12/04/15 | 12/11/15 | RECEIVED Ordered for Olive KG
Electronic | EL-MS0360 | Noninsulated Wire Ferrule,16 AWG, | Fastenal | 749649 | Mouser | 644-F78-8-M | 1 | ea | $0.06 | $0.06 | 3,050 | PO12004 | 02/12/16 | 02/19/16 | RECEIVED 10,000 OLIVE ORDERED, FASTENAL KG 1/26 Eric approved EL-MS0360 ferrule, used on the diode inside the chassis
Electronic | EL-MS0010 | Heavy Duty Power Connectors POWERPOLE 15A CONT | Anderson Power Connectors | 1332-BK | Sager | 879-1332-BK | 6 | ea | $0.10 | $0.57 | 18,300 | PO11661 | 02/05/16 | 03/08/16 | RECEIVED. OLIVE PO DELIVERY 2/29 KG NUTMEG ordered from Mouser, Sager 4 week leadtime for OLIVE.
Electronic | EL-MS0008 | Heavy Duty Power Connectors HOUSING ONLY, BLACK POWERPOLE 15/45 | Anderson Power Connectors | 879-1327G6-BK | Sager | 879-1327G6-BK | 6 | ea | $0.19 | $1.15 | 18,300 | PO11065 | 12/07/15 | 12/10/15 | Ordered for Olive KG
Electronic | EL-FA0033 | Pelonis FAN 24V 80x15mm Low flow | Pelonis | C8015L24BPLP1b-7 | Pelonis | C8015L24BPLP1b-7 | 1 | ea | $3.12 | $3.12 | 3,050 | PO11299 | 12/30/15 | 02/05/16 | Delivery 3/17 KG Switching to pelonis alternate – Nutmeg built with free samples. Olive is on this PO11299.TS
Electronic | EL-WR0040 | Wire - Single Conductor 20AWG SOLID PTFE, RED | Alpha Wire | 2856/1 | Allcable |  | 175 | mm | $0.00 | $0.64 | 533,750 | PO12258 | 03/01/16 | 04/07/16 | Received 500' will receive balance 1300 ft April 4NEED 1751' FOR OLIVE / Allcable 7-10 day leadtime $ 1.12 ft 100 ft =$112.00 We want 3112010 TN005 for Nutwort/Olive | ERIC WILL EVALUATE WHAT ALL CABLE SAMPLES
Electronic | EL-MS0346 | MOD PWR ENTRY INLET W/FUSE 6A - IEC C14 Receptacle – AC Filter 6A 250VAC | Shaffner | FN9260-6-06 | Sager | FN9260-6-06 | 1 | ea | $4.76 | $4.76 | 3,050 | PO11031 | 12/03/15 | See notes | Received Sager 2000 pc stock $4.76ea, 12 weeks. Ordered for Olive.KG
Electronic | EL-MS0347 | FUSE CERAMIC 6.3A 250VAC 5X20MM | Littlefuse | 023406.3MXP | Mouser & TTI | 023406.3MXP | 2 | ea | $0.37 | $0.74 | 6,100 | PO11016, 10936 | 12/03/15 | 02/05/16 | Mouser PO11016 = 2/5/16 delivery. TTI PO10936, quoted 12 wk leadtime-no stock – for Olive 2/5/16 KG - New delivery date on this item is ~ Feb. 22 – these have 12-14 week lead time. TS/KG ARROW STOCK IMMEDIATELY AVAILABLE.
Electronic | EL-PS0031 | Mean Well Switching Power Supplies 504W 24V 21A Power Supply W/PFC | Mean Well | RSP-500-24 | Sager | 709-RSP500-24 | 1 | ea | $65.00 | $65.00 | 3,050 | PO08321 | 06/26/15 | See notes | We have scheduled deliveries on these PSU's until Aug. 2016
Electronic | EL-MS0133 | CONN, RCPT, 14 POS w/Brass Inserts | TE Connectivity AMP Connectors | 211103-1 | TTI | 211103-1 | 1 | ea | $3.12 | $3.12 | 3,050 | PO11064 | 12/07/15 | 12/09/15 | Received Min 1 / 1 Ordered for Olive KG - EL-MS0131 landed on the PO in error. Kim is getting with Lisa to fix to correct part number. TS
Electronic | PC-CN0032 | Term Block Plug 2POS STR 5.08MM | Molex | 395300002 | TTI | 395300002 | 5 | ea | $0.41 | $2.03 | 15,250 | PO10936 | 12/03/15 | See notes | Received TTI Check lead time with vendor and order accordingly. TS Ordered for Olive. KG
Electronic | EL-MS0124 | 20-24 AWG Tin Sockets for Receptacle - 4K Reel | TE Connectivity AMP Connectors | 1-66331-4 | TTI -DIGIKEY | 1-66331-4 | 13 | ea | $0.21 | $2.70 | 39,650 | PO11026, 10936 | 12/07/15 | See notes | Digikey, 4k min PO11026 = Nutmeg / TTI 6 wk leadtime PO10936 = Olive.KG
Electronic | PC-CN0056 | Headers & Wire Housings 20 CKT CRIMP HOUSING Female | Molex | 50-57-9420 | TTI | 538-50-57-9420 | 1 | pcs | $0.44 | $0.44 | 3,050 | PO10936 | 12/03/15 | See notes | TTI stock available - Ordered for Olive. KG
Electronic | PC-CN0003 | Molex - CONN HOUSING 3POS .100 W/LATCH | Molex | 50579403 | Sager | WM2901-ND | 7 | ea | $0.05 | $0.36 | 21,350 | PO11065 | 12/08/15 | 12/11/15 | Partial short shipped, will ship week of 3/15Ordered for Olive KG1800 m/m 0.0514
Electronic | EL-MS0342 | FERRITE TUBULAR BEAD 7.87MM RoHS Status | Laird Technologies - Signal Integrity Products | 28B0625-100 | Sager | 240-2115-ND | 1 | ea | $0.23 | $0.23 | 3,050 | PO11661 | 02/05/16 | 03/08/16 | ORDERED FOR OLIVE KGOrdered for Nutmeg only Digikey 0.468 ea mouser stock 0.70ea future no quote,
Electronic | PC-CN0054 | Headers & Wire Housings HSG 12P Female SINGLE ROW POSITIVE LATCH | Molex | 50-57-9412 | TTI | 538-50-57-9412 | 1 | pcs | $0.17 | $0.17 | 3,050 | PO11727 | 02/05/16 | 03/03/16 | Received OLIVE Ordered KG
Electronic | EL-MS0336 | Ferrite Cable Cores 310ohms 100MHz 7mm Inside Dia. | Laird Technologies - Signal Integrity Products | 28B0616-000 | Mouser | 28B0616-000 | 1 | ea | $0.29 | $0.29 | 3,050 | PO11016 | 12/07/15 | 02/05/16 | Mouser confirmed 2/5/16 delivery KG 12 wk leadtime sager 50 Ship 12/ 5 & 3050 ship 1/4/2016. Ordered for Olive.KG
Electronic | PC-CN0058 | Connector housing, 16 pin femaleFemale 16 pin Molex connector housing | Molex | 50-57-9416 | TTI | 538-50-57-9416 | 1 | pcs | $0.33 | $0.33 | 3,050 | PO10936 | 12/03/15 | See notes | Received TTI has stock on hand kg Sager 6 Weeks lead time TS. Ordered for Olive. KG
Electronic | EL-MS0343 | Ferrite 10.16mm ID for 16 pin Y&Z connector | Laird Technologies - Signal Integrity Products | 28B0735-000 | Sager | 28B0735-000 | 1 | ea | $0.26 | $0.26 | 3,050 | PO11661 | 02/05/16 | 03/08/15 | ORDERED FOR OLIVE K order for Nutmeg Digikey, Future for Olive
Electronic | PC-CN0060 | Female 10 pin Molex Connector Housing | Molex | 50-57-9410 | TTI | 538-50-57-9410 | 1 | pcs | $0.18 | $0.18 | 3,050 | PO10936 | 12/03/15 | See notes | TTI stock on hand kg 5 Weeks lead time. TS Ordered for Olive. KG
Electronic | EL-MS0332 | Ferrite Cable Cores 220ohms 100MHz 5mm I.D. | Laird Technologies - Signal Integrity Products | 28B0434-000 | Mouser / Sager | 28B0434-000 | 2 | ea | $0.15 | $0.29 | 6,100 | PO11016 | 12/03/15 | See notes | Received Mouser confirmed 2/5 delivery KGOrdered Stock at Mouser, Sager 10 Weeks lead time. TS Ordered for Olive.KG
Electronic | EL-MS0344 | Ferrite Tubular Bead 5.90mm | Laird Technologies - Signal Integrity Products | 28B0591-200 | Sager Digikey | 28B0591-200 | 1 | ea | $0.34 | $0.34 | 3,050 | PO11661 | 02/05/16 | 04/10/16 | OLIVE 3,520 SAGER PO 11661 = 500 3/17/16 balance ~ 4/15, DIGIKEY STK AVAIL, IF DELIVERY does not meet demand. KG 12 wk leadtime SAGER Ordered Digikey for Nutmeg only KB
Electronic | EL-MS0329 | TVS Diode – 1500W, 5V Reverse Standoff, 6V Breakdown, 9.4V Clamp, 200A Surge | ON Semiconductor | 1N6373G | Mouser / Future /Digikey | 1N6373G | 1 | ea | $0.24 | $0.24 | 3,050 | PO10116, 11026 | 12/07/15 | 12/10/15 | Received Digikey PO11026 = Olive (shipping 2005 12/7 backorder 995 pcs 12/11/15) Mouser 11016 = Nutmeg Future quote 4 wks leadtime 0.178 ea 500 /500 min mult. Weeks lead time. TS sager not francshised.KG
Electronic | EL-MS0247 | Heat shrink Tubing – 0.19-0.09 – Black, 100' | EDC – Electronics Distributors Corporation | 88-01870 | McMaster-Carr | 7856K74 | 40 | mm | $0.01 | $0.20 | 122,000 | PO11684 / PO12659 | 02/01/16 | 04/11/16 | Ordered PO12659 to replace TL- CS0129 , CS0083OLIVE 500' EDC Tubing approved, by Eric K KG 100' =$22.08/100'
Electronic | EL-CA0078 | Flat Cables .050" 10C 10 COLOR 28AWG STRANDED | TE Connectivity AMP Connectors | 3302/10-300 | TTI | 517-3302/10-300 | 360 | mm | $0.02 | $5.91 | 1,098,000 | PO12454, PO10936 | 12/03/15 | See notes | Received Ordered for Olive. KG Mouser met TTI cost, stock available at Mouser = 13 of 300' NUTMEG $76.17 per 300' KG 2x180mm 4 Weeks lead time. TS
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

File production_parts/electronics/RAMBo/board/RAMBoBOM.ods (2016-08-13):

Parts | Qty | Value | Device | Package | Description | Manufacturer | mfr part #
S1 | 1 |  | 31-XX | B3F-31XX | SWITCH, TACTILE, SPST-NO, 50mA, THD | Omron | 1571610-2
JP3, X35, X36, X37, X38 | 1 |  | M02PTH | 1X02 | 1x2 header |  | 2211S-02G
C31, C36, C41, C46, C51 | 5 | 0.22uF | C-EUC0603 | C0603 | 0.22uF 100V capacitor X or 15% | Yageo | CC0603KRX7R7BB224
R12, R17, R18, R22, R26 | 5 | 0r | R-US_R0603 | R0603 | 0r (zero ohm) 100mW 5% resistor | Bourns | CR0603J000ELF
R4, R7, R8, R10, R14, R15, R19, R20, R23, R24 | 10 | 0r1 | R-US_R1206 | R1206 | 0r1 (0.1ohm) .5mW 1% resistor | Bourns | CRM1206-FX-R100ELF
R40, R41, R50, R55, R58, R69 | 6 | 1.8K | R-US_R0603 | R0603 | Resistor, Thick Film, 1.8K Ohm, 50V, 5±%, 100ppm, 0603 Case Size |  | RC0603JR-071K8L
R43, R49, R52, R54, R57, R59, R60, R61, R62, R63, R71 | 11 | 100K | R-US_R0603 | R0603 | 100Kohm 100mW 1% resistor | Yageo | RC0603FR-07100KL
C6, C7, C8, C9, C10, C11, C14, C15, C26, C52, C3, C4, C17, C18, C23, C24, C27, C28, C29, C32, C33, C34, C37, C38, C39, C42, C43, C44, C47, C48, C49, C55, C56, C59, C64, C71, C72, C73, C74, C75, C25, C60, C62 | 43 | 100nF | C-EU0603-RND | C0603-ROUND | 0.1uF 50V capacitor | Kemet | x16
C65, C66 | 2 | 100uF | CPOL-USE3.5-8 | E3,5-8 | Aluminum Electrolytic Capacitors - Leaded 100uF 50V 20% 105c | Nichicon | UVZ1H101MPD1TD
R44, R45, R46, R47, R73 | 5 | 10K | R-US_R0603 | R0603 | 10Kohm 100mW 1% resistor | Panasonic | ERJ-3EKF1002V
C35, C53, C54 | 3 | 10nF | C-USC0603 | C0603 | 10nF (0.01uF) 25V capacitor | TDK | C1608X7R1E103K080AA
R42, R48, R51, R53, R56, R70 | 6 | 10r | R-US_R0603 | R0603 | 10r (10ohm) 100mW 1% resistor | Vishay | CRCW060310R0FKEA
C30 | 1 | 10uF | C-EUC1210K | C1210K | Multilayer Ceramic Capacitors MLCC - SMD/SMT 1210 10uF 25volts X5R 10% | TDK | C3225X5R1E106K
C2 | 1 | 10uF | C-USC0805 | C0805 | 10uF | Kemet | C0805C106K8PACTU
C45 | 1 | 10uF | C-USC2220K | C2220K | 10uF | TDK | C5750X7R1H106M230KB
Y1, Y2 | 2 | 16MHz KX-7 | CRYSTAL-3.2-2.5 | CRYSTAL-3.2-2.5 | 16MHz KX-7 10ppm crystal | TXC | 7M-16.000MEEQ-T
R33, R34, R35 | 3 | 1K | R-US_R0603 | R0603 | RESISTOR, THICK FILM, 1KOHM, 100mW, 1% | Panasonic | ERJ-3EKF1001V
R72 | 1 | 1M | R-US_R0402 | R0402 | RES 1M OHM 1/10W 5% 0402 SMD | Panasonic | ERJ2GEJ105X
D11, D13, D14, D15, D16, D17, D18, D19 | 8 | 1N4148WT | 1N4148WT | SOD523 | Diode Small Signal Switching 75V 2-Pin SOD-523F T/R | Fairchild | 1N4148WT
RN5 | 1 | 1k | 4R-NCAY16 | CAY16 | Resistor Networks & Arrays 1K 5% Convex 4resistors | Bourns | CAY16-102J4LF
C16 | 1 | 1uF | C-EU0603-RND | C0603-ROUND | 1uF 10V capacitor | yageo | CC0603ZRY5V6BB105
C40 | 1 | 1uF | C-USC0805 | C0805 | Multilayer Ceramic Capacitors MLCC - SMD/SMT 1.0UF 50V 10% 0805 | Murata | GRM21BR71H105KA12L
R1, R2 | 2 | 22R | R-US_R0402 | R0402 | 22R (22ohm) 62.5mW 1% resistor | Yageo | RC0402FR-0722RL
C1, C12, C13, C57, C58 | 5 | 22pF | C-EU0603-RND | C0603-ROUND | 22pF 50V capacitor | TDK | C1608C0G1H220J
R30 | 1 | 3.3K | R-US_R0603 | R0603 | RESISTOR, THICK FILM, 3.3KOHM, 100mW, 5% | panasonic | erj3geyj332v
X16 | 0 | 32u2 EXT | M08X2 | 2X8 | 2x8 header
L3 | 1 | 33uH | L-USNR8040 | NR8040 | Fixed Inductors 33uH | TDK | VLP8040T-330M
X17, X18 | 2 | 3x2M | PINHD-2X3 | 2X03 | 2x3 header |  | 2213S-06G
C63 | 1 | 4.7nF | C-EUC0402 | C0402 | Multilayer Ceramic Capacitors MLCC - SMD/SMT 4.7nF 25V X7R 10% |  | CC0402KRX7R8BB472
R3 | 1 | 470K | R-US_R0603 | R0603 | SMD 1/10watt 470Kohms 1% Thick Film Resistors | Vishay | CRCW0603470KFKEA
C76 | 1 | 470uF | CPOL-USC12,5-5 | C12,5-5 | CAPACITOR ALUM ELEC, 470UF, 50V, 20%, RADIAL | nichicon | UPW1H471MHD1TO
 | 0 |  |  |  | Alternate capacitor |  | UVZ1H471MHD1TO
R27, R28, R31, R32, R36, R37, R38, R39 | 8 | 4K7 | R-US_R0603 | R0603 | 4K7 (4.7Kohm) 100mW 1% resistor | Panasonic | ERJ3EKF4701V
R29, R65, R66, R67, R68 | 5 | 56r | R-US_R0603 | R0603 | RESISTOR, THICK FILM, 56OHM, 100mW, 5% | Vishay | CRCW060356R0JNEA | Till 05/22/2014 | 200bds w/drivers
U5, U6, U7, U8, U9 | 5 | A4982 | A4982QFN32ROUNDPADS | QFN32TROUND | A4982 | Allegro | A4982SETTR-T | 2100 | 6500 | 325
U4 | 1 | AD5206 | AD5206 | TSSOP24 | AD5206 (IC) | Analog Devices | AD5206BRUZ10-RL7 |  | currently 300bd/wk
U10 | 1 | ADUM7441 | ADUM7441 | QSOP16 | ADUM7441 | Analog Devices | ADUM7441ARQZ-RL7
U2 | 1 | ATMEGA2560-16AU | ATMEGA25602560-16AU | TQFP100 | ATMEGA2560-16AU (IC) | Atmel | ATMEGA2560-16AUR
U1 | 1 | ATMEGA32U2-MUR | ATMEGA16U2-MU | MLF32 | ATMEGA32U2-MUR (IC) | Atmel | ATMEGA32U2MU
D1, D3, D6, D10 | 7 | B240A-13-F | SCHOTTKY-DIODE | SMA-SM | 3.0A 100V Diode | Diodes Inc. | SK310A-TP
X1, X3, X5, X9, X27, X28, X29, X30 | 6 | C-GRID-02-70543 | C-GRID-02-70543 | 70543-02 | WIRE-BOARD CONNECTOR HEADER 2POS, 2.54MM | Molex | 70543-0001
X21, X22, X23, X24, X25, X26 | 6 | C-GRID-03-70543 | C-GRID-03-70543 | 70543-03 | WIRE-BOARD CONNECTOR HEADER 3POS, 2.54MM | Molex | 70543-0002
X4, X6, X7, X8, X10, X14, X15 | 7 | C-GRID-04-70543 | MPT4 | 4POL254 | WIRE-BOARD CONNECTOR HEADER 4POS, 2.54MM | Molex | 70543-0038
L2 | 1 | 10uH | L-US | C0805 | INDUCTOR 10UH 20% 0805 SMD | Taiyo Yuden | CBC2012T100M
D4, D5 | 2 | CD1206-S01575 | DIODE-MINIMELF | MINIMELF | 100V 150mA diode | Bourns | CD1206-S01575
Z1, Z2 | 2 | CG0603MLC-05E | VARISTORCN0603 | CT/CN0603 | 5V 20V varistor | Bourns | CG0603MLC-05E
X13 | 1 | EXT-2 | M10X2 | 2X10 | 2x10 header |  | 2213S-20G
F4 | 1 | FUSE | FUSE | FUSE-ATO-SMD | FUSE HOLDER, AUTO BLADE, SMT | Keystone | 3587TR
D40 | 1 | RSB39VTE-17 | PINHD-1X1 | SOD323 | TVS DIODE 30VWM SOD323 |  | RSB39VTE-17
D9, D21, D22, D23, D24, D25, D26, D27, D28, D29, D30, D31, D32, D33, D34, D35, D36, D37, D38, D39 | 20 | GND | PINHD-1X1 | 1X01 | TVS DIODE 30VWM SMD |  | SMAJ30A
C67, C68, C69, C70 | 4 | 100nF | C-EU0603-RND | C0402 | CAP CER 0.1UF 16V 10% X7R 0402 |  | GRM155R71C104KA88D
LED7 | 1 | GREEN | LEDCHIP-LED0805 | CHIP-LED0805 | GREEN LED |  | 598-8170-107F
Q4, Q8 | 2 | IRLML6346TRPBF | MOSFET-NCHANNELSMD | SOT23-3 | N CH MOSFET, 30V, 3.4A, 3-SOT-23 |  | IRLML6346TRPBF
U3 | 1 | LM22675 | LM22675 | SOIC127P600X170-9N | IC REG BUCK 5V 1A 8SOPWRPAD |  | LM22675
X20 | 1 | M05PTH | M05PTH | 1X05 | 1x5 |  | 2211S-05G
X39, X32 | 2 | M05X2PTH | M05X2PTH | AVR_ICSP | 2x5 header |  | 2213S-10G
F1 | 1 | MF-MSMF050-2 500mA | L-EUL1812 | L1812 | 500mA 15V fuse ptc reset | Bourns | MF-MSMF050-2
X33 | 1 | MSTBA6 | MSTBA6 | MSTBA6 | 6 pin fixed terminal block | Molex | 39532-1006
X11 | 1 | MSTBV10 | MSTBV10 | MSTBV10 | CONN HEADER 10POS 5.08MM STR TIN | Molex | 395311010
R11, R13 | 0 | NP | R-US_R0603 | R0603
F2, F3 | 2 | OMNI-BLOK | OMNI-BLOK | OMNI-BLOK | 5A fuse/fuse block | Littlefuse | 0154005.DR
Q1, Q2, Q3, Q5 | 4 | PSMN7R0-60YS | PH7030L | SOT669 | PH7030L (Mosfet) 60V 356A 117W | NXP | PSMN7R0-60YS,115
X34 | 1 | PWM_EXT | M06SIP | 1X06 | 1x6 header |  | 2213S-06G
LED2, LED3, LED4, LED5, LED6, LED8 | 6 | RED | LEDCHIP-LED0805 | CHIP-LED0805 | RED | Dialight | 5988110107F
D7 | 1 | S3A | DIODE-D0-214AB | DO-214AB | 3A 50V Diode |  | S3A
X12, X40 | 2 | SPI | M04X2 | 2X4 | M04X2 |  | 2213S-08G
D12 | 1 | SZMM3Z4V7T1G | ZENER-DIODESOD323 | SOD323-R | Zener Diodes ZEN REG 0.2W 4.7V |  | SZMM3Z4V7T1G
X2 | 1 | USB B-TH | PN61729 | PN61729 | USB B-TH connector | FCI | 61729-0010BLF
LED1, LED9, LED10 | 3 | YELLOW | LEDCHIP-LED0805 | CHIP-LED0805 | YELLOW LED | Dialight | 5988140107F
CF1, CF2, CF3, CF4, CF5, CF6, CF7, CF8, CF9, CF10, CF11, CF12, CF13, CF14, CF15, CF16, CF17, CF18, CF19, CF20 | 20 |  |  |  | EMI Filter 2A 50VDC Flat Style SMD |  | NFM21CC223R1H3D
L1, L4 | 2 |  |  |  | FERRITE CHIP 60 OHM 6000MA 1806 |  | BLM41PG600SN1L
D9, D21, D22, D23, D24, D25, D26, D27, D28, D29, D30, D31, D32, D33, D34, D35, D36, D37, D38, D39 | 20 |  |  |  | TVS DIODE 30VWM 48.4VC SMA |  | SMAJ30A
PCB | 1 |  |  |  | PCB | UltiMachine | UMRAMBOPCB1.3L
White Wire | 0.012 |  |  |  | white wire |  | 1853 WH001
Black Wire | 0.008 |  |  |  | black wire |  | 1853 BK001
loose gold connectors | 34 |  |  |  | CONTACT, FEMALE, 30-24AWG, CRIMP | molex | 16-02-0097
replacement fuses | 0 |  |  |  |  |  | 0448005.MR
2pos 5.08mm Pluggable | 5 |  |  |  | TERMINAL BLOCK, PLUGGABLE, 2 POS, 24-12AWG | Molex | 39530-0002
6pos 5.08mm Pluggable | 1 |  |  |  | TERMINAL BLOCK PLUGGABLE, 6POS, 24-12AWG | Molex | 39530-0006
gold crimp on reel | 10 |  |  |  | GOLD CONTACT, FEMALE, 30-24AWG, CRIMP | Molex | 16020082
15A ATO fuse | 1 |  |  |  | ATO fuse 15A | Littelfuse | 0287015.PXCN
4P POSITIVE LATCH | 6 |  |  |  | WIRE-BOARD CONNECTOR RECEPTACLE, 4POS, 2.54MM | Molex | 50-57-9404
3P POSITIVE LATCH | 3 |  |  |  | WIRE-BOARD CONNECTOR RECEPTACLE, 3POS, 2.54MM | Molex | 50-57-9403
2P POSITIVE LATCH | 3 |  |  |  | WIRE-BOARD CONNECTOR RECEPTACLE, 2POS, 2.54MM | Molex | 50-57-9402
ULTRA-FAST RECEPT | 6 |  |  |  | TERMINAL FEMALE DISCONNECT 3.18MM VIOLET | TE | 7-520366-2
microswitches | 3 |  |  |  | microswitches | Omron | SS-3GL13PT
microswitches | 0 |  |  |  | microswitch flat | Omron | SS-3GLPT
USB A-B cable | 1 |  |  |  | USB A-B cable
X11 | 0 | MSTBV10 | MSTBV10 | MSTBV10 | TERMINAL BLOCK EUROSTYLE 10POS, 26-14AWG | multicomp | MB612-50810

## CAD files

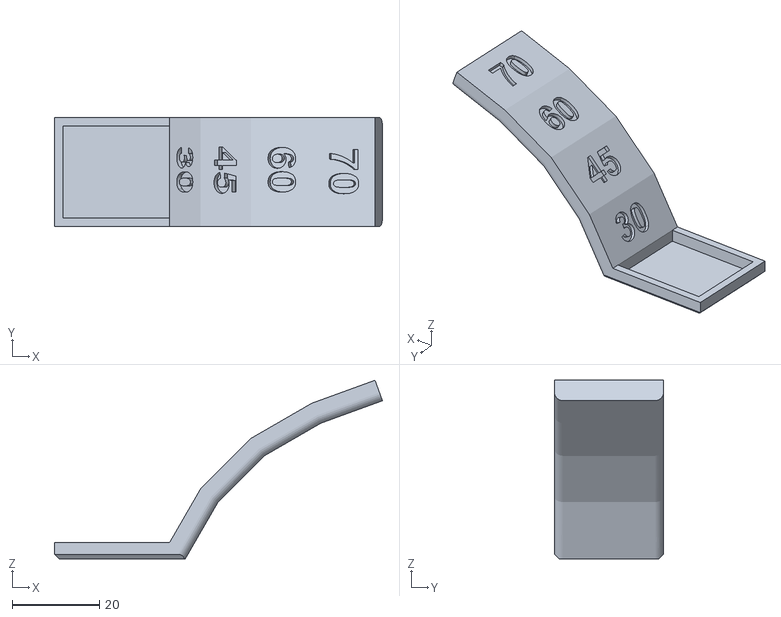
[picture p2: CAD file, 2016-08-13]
documentation/sample_prints/benchmarks/make_2015_tests/overhang_test.stl
75.2 x 25.0 x 40.9

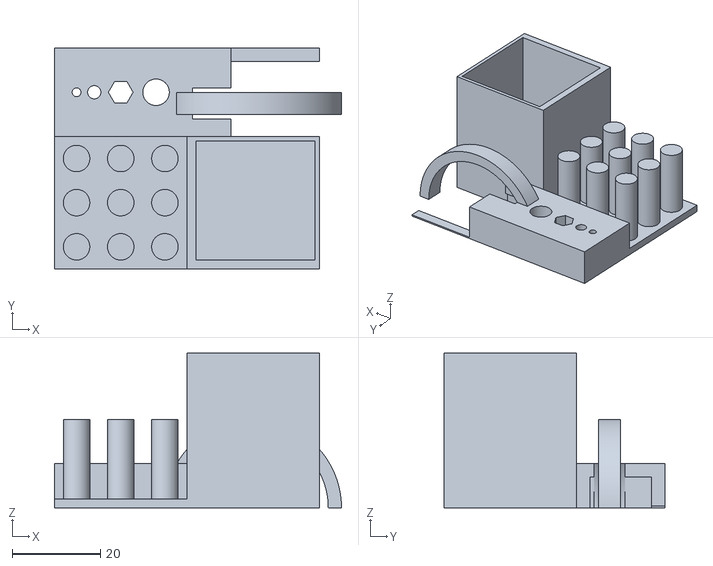
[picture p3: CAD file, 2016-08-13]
documentation/sample_prints/benchmarks/make_torture_test/torture_test.stl
65.0 x 50.0 x 35.0

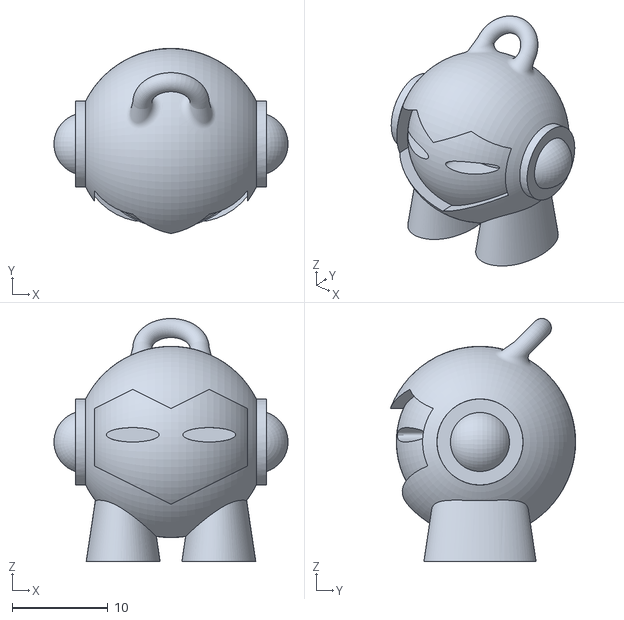
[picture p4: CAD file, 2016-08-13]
documentation/sample_prints/benchmarks/marvin_keychain/marvin_keychain.STL
24.5 x 19.4 x 25.4

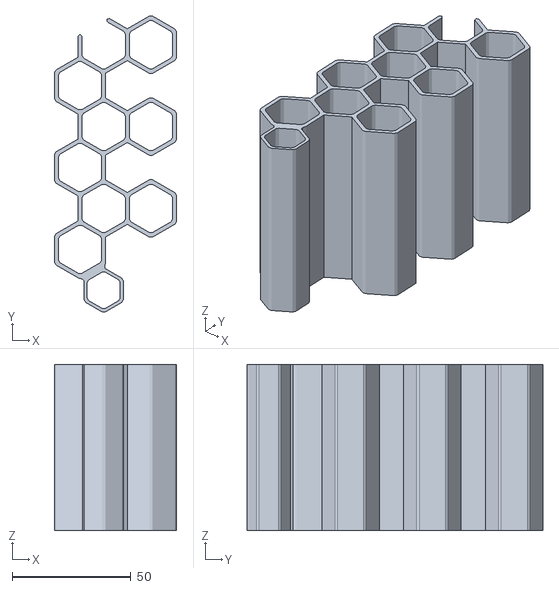
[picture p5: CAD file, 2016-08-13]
documentation/sample_prints/functional/mobile_device_rack/stand_3.stl
51.5 x 124.8 x 70.0

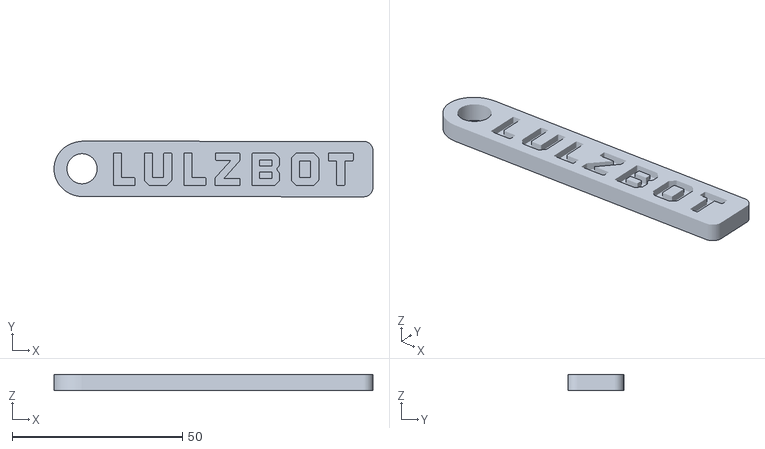
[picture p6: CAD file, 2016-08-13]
documentation/sample_prints/LulzBot/LulzBot_keychain/LulzBot_keychain.stl
93.7 x 16.3 x 4.80

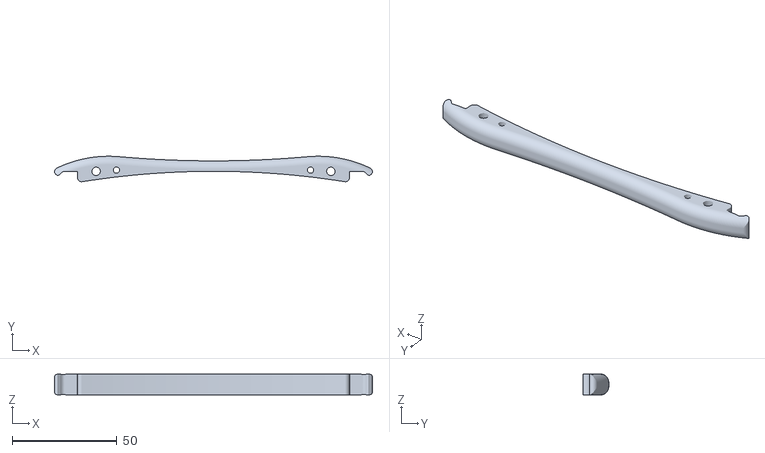
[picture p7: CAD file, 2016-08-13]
documentation/sample_prints/modifications/spool_mount/spool_mount.STL
152.0 x 12.2 x 10.0

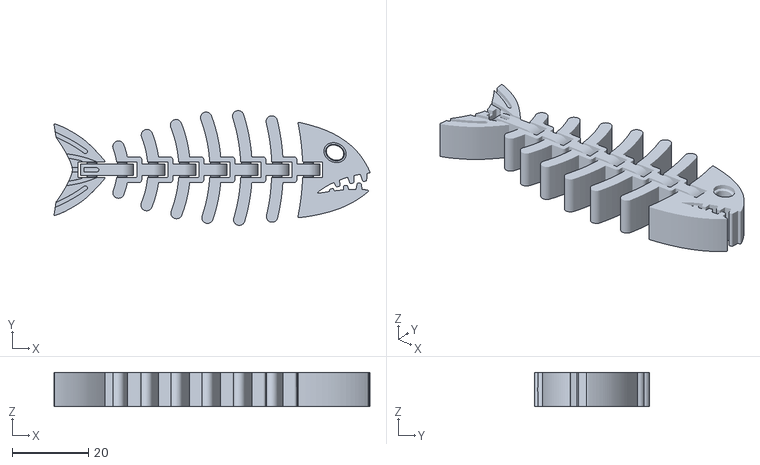
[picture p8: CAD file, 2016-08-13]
documentation/sample_prints/novelties/fish_fossilz/fish_fossilz.stl
82.8 x 30.1 x 9.00

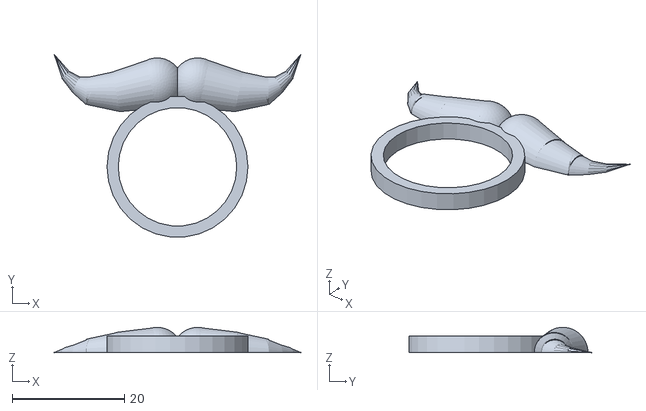
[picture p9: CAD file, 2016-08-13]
documentation/sample_prints/novelties/mustache_ring/mustache_ring.stl
43.9 x 32.5 x 4.50

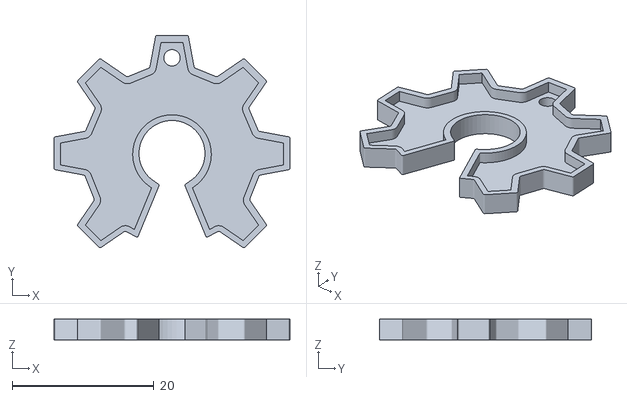
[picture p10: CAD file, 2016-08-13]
documentation/sample_prints/novelties/OSHW_logo/OSHW_logo.stl
33.3 x 30.0 x 2.94

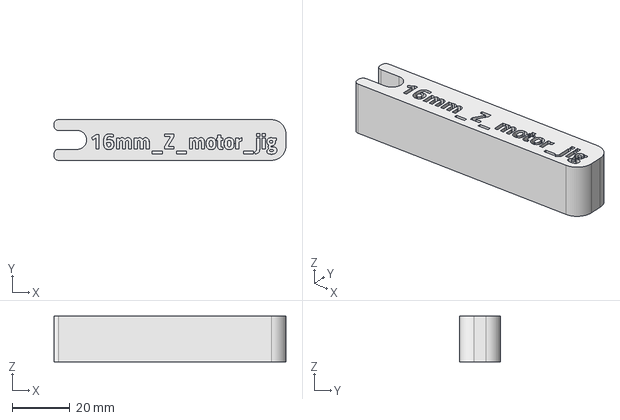
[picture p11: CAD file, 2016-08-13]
production_parts/jigs/16mm_coupler_spacer_Z_axis_v0.1.fcstd
80.0 x 14.0 x 15.8 mm

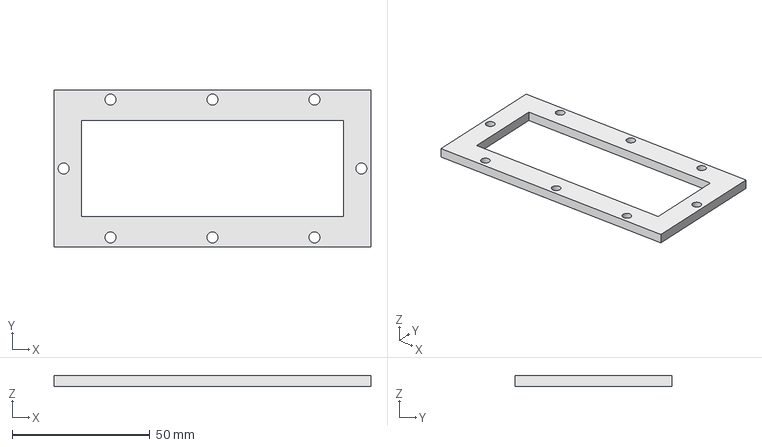
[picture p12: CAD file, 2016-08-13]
production_parts/jigs/control_box_test_fixture/control_box_test_fixture_top_plate.fcstd
115.0 x 57.0 x 4.00 mm

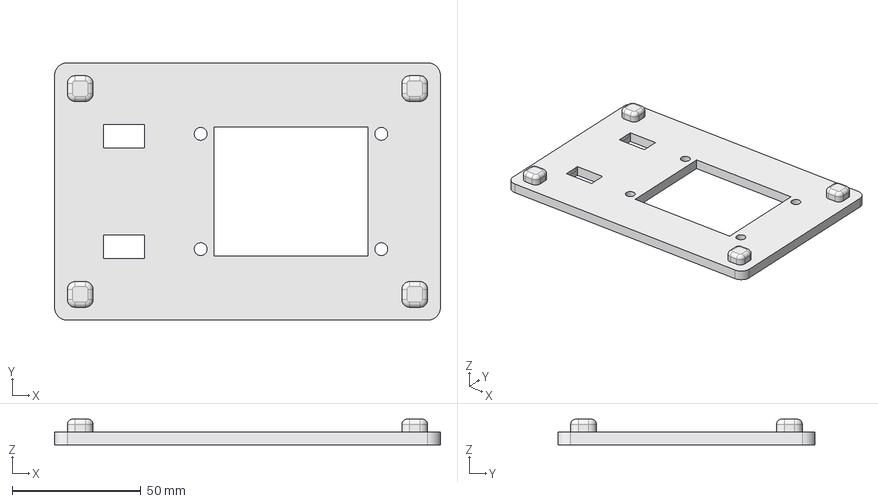
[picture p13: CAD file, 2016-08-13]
production_parts/jigs/harness_test_fixture/taz_heat_bed_external_harness_v2.fcstd
150.0 x 100.0 x 10.0 mm

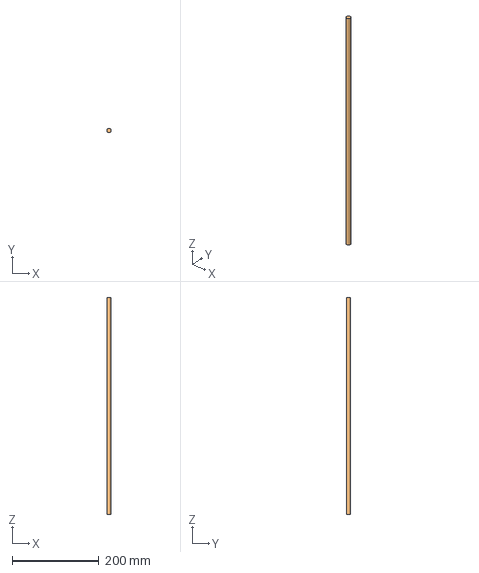
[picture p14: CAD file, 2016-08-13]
production_parts/machined_parts/10_12_mm_smooth_rods/10mmx500mm_rod_v0.1.fcstd
9.99 x 10.00 x 500.0 mm

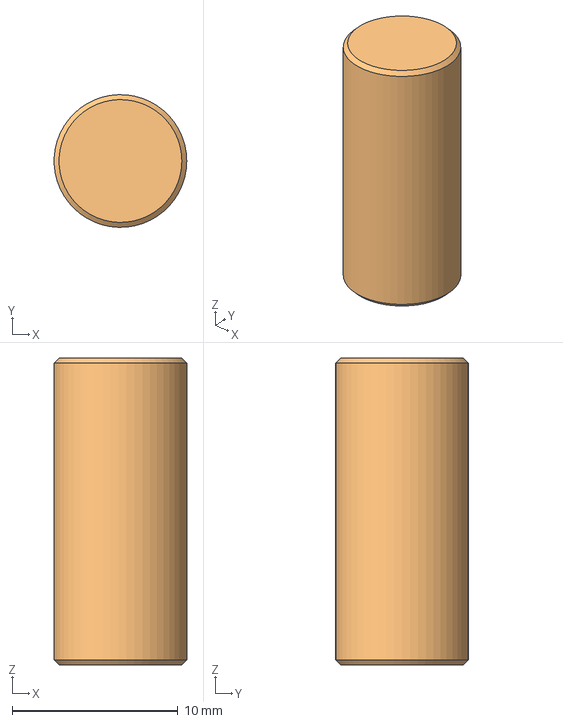
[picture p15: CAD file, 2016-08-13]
production_parts/machined_parts/8_mm_rod/8mmx18-19mm_rod_v0.1.fcstd
7.99 x 8.00 x 18.5 mm

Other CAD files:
production_parts/machined_parts/bed_plate_v5.0/bed_plate_v5.0.FCStd
production_parts/machined_parts/corner_bracket_v2.0/corner_bracket_v2.0.1.FCStd
production_parts/machined_parts/electronics_chassis/electronics_cover_v04.1.fcstd
production_parts/machined_parts/electronics_cover/electronics_cover_revA.step
production_parts/printed_parts/herringbone_large_gear/source/Herringbone_gears.scad
production_parts/printed_parts/herringbone_large_gear/source/Herringbone_gears_hi-res.scad
production_parts/printed_parts/herringbone_large_gear/source/Herringbone_gears_hi-res_chamfer.scad
production_parts/printed_parts/herringbone_small_gear/source/Herringbone_gears.scad
documentation/sample_prints/benchmarks/make_2015_tests/XY_resonance_1.0mm_walls.stl
documentation/sample_prints/benchmarks/make_2015_tests/XY_resonance_test.stl
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

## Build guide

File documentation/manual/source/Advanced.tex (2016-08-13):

%
% Advanced.tex
% Advanced Techniques
%
% LulzBot® TAZ User Manual
%
% Copyright (C) 2015 Aleph Objects, Inc.
%
% This document is licensed under the Creative Commons Attribution 4.0
% International Public License (CC BY-SA 4.0) by Aleph Objects, Inc.
%
%

\section{\texttt{Intro}}
\index{advanced techniques}
\glossary{3D Printer}{Also referred to as additive manufacturing, is the process of fabricating objects from 3D model data, through the deposition of a material in accumulative layers.}
\glossary{Spool}{Plastic filament coiled and stored on a plastic reel. Preferred over 1.75mm filament due to improved feeding and better mounting options.}
\glossary{Filament}{Plastic material in a ``string'' like form, as it is fed to the printer.}
\glossary{ABS}{Acrylonitrile butadiene styrene thermoplastic. Usually extrudes at 230°C with the Budaschnozzle and 240°C - 250°C with the LulzBot Hexagon Hot End.}
\glossary{PLA}{Polylactic acid is a corn-based biodegradable polymer. Usually extrudes at \texttt{185°C} with the Budaschnozzle and \texttt{205°C} with the LulzBot Hexagon Hot End.}
\glossary{HDPE}{High-density polyethylene.}
\glossary{Polycarbonate}{A strong and impact-resistant thermoplastic. Usually extrudes at ~\texttt{300°C}.}
\glossary{HIPS}{High-impact polystyrene. Usually extrudes at \texttt{230°C} with the Budaschnozzle and \texttt{230°C} with the LulzBot Hexagon Hot End}
\glossary{Laywoo-D3}{Wooden filament similar to PLA. Forty percent of its content consists of recycled wood. Usually prints at ~\texttt{180°C} to \texttt{210°C}. Color can be changed by varying the extrusion temperature.}
After you become familiar with printing using the default settings, a few advanced techniques may help in getting better and more consistent prints from the LulzBot\textsuperscript{\miniscule{\textregistered}} TAZ 3D printer. Some of these instructions are items and materials not included with the TAZ. With any of these additional items or materials, follow safety and usage guidelines as instructed by the manufacturer.

\section{\texttt{Changing nozzles}}
\index{nozzle}
\glossary{Nozzle}{The metal tip at the bottom of the hot end. It has a small hole where the plastic filament comes out of the printer.}
\glossary{Layer height}{The thickness of each individual deposited layer of the three-dimensional model when cut with a slicing program.}
\index{high resolution}
\textcolor{red}{Nozzle related issues will not be covered under warranty after nozzle changes}.

Your hot end is equipped with a 0.50mm nozzle. This nozzle diameter will print faster than a 0.35mm nozzle. Purchase a tool head from \texttt{LulzBot.com} with an alternate nozzle diameter for quick, easy, and simple changes.

Due to the specific torque of 30 inch pounds required to tighten the nozzle when removed, removing the nozzle is not recommended. Failure to properly tighten the nozzle to the specific recommended torque may lead to leaks or damage if over-tightened.

\index{hot end}
\glossary{Hot end}{The hot end is the whole part where the plastic melts, including the nozzle, heater block, thermistor, and heat sink. The LulzBot Hexagon Hot End comes standard on the TAZ 5.}
\index{threaded extension}
\glossary{Threaded extension}{Used to separate the heater block and nozzle from the PEEK insulator. The plastic filament passes through the threaded extension into the melting chamber.}
%\glossary{PEEK}{Polyether ether ketone: an organic polymer used to insulate the hot end due to its mechanical properties at elevated temperatures.}
%In most cases the nozzle is best changed when the hot end is slightly warm. NEVER try to remove the nozzle when the hot end is at extrusion temperature. At higher temperatures the threaded extension expands in the nozzle causing the nozzle to bind if turned. Heat the hot end to \texttt{160°C}. This will soften the plastic inside the hot end and allow the nozzle to be loosened off the threaded extension. Power off the printer and before it cools unscrew the nozzle. Take care when removing the nozzle while the hot end is hot. Wear leather gloves or use a towel to turn the nozzle off the hot end.

%\index{wrench}
%\index{heater block}
\glossary{Heater block}{Machined from aluminum, the heater block generates heat with a heater resistor and uses a thermistor to measure the temperature.}
\glossary{Thermistor}{A special type of resistor that changes resistance based on temperature. It is used to measure temperature on the nozzle and the heated bed.}
\glossary{Heater resistor}{A special type of resistor that is used to apply heat in a small area.}
%The LulzBot Hexagon does not currently have additional nozzle sizes. If a nozzle change is required you will need to tighten the nozzle to the recommended 30in/lb of torque.

%Prior to any modifications make sure the that printer is unplugged from both the wall and the computer. Use a 7mm wrench to turn the nozzle and a 18mm wrench to hold the heater block. A guide on assembling the LulzBot Hexagon hot end is available at \texttt{http://ohai-kit.alephobjects.com}

%\index{anti-seize}
%If you will be changing nozzles frequently we suggest reapplying a small amount of high temperature anti-seize compound to the inside threads of the nozzles. You will need an anti-seize capable of temperatures of at least \texttt{250°C}.

\section{\texttt{Bed Adhesion}}
\index{warping}
\index{bottle}
\index{Ninjaflex}
\index{Nylon}
\index{brim}
\index{PEI}
\index{IPA}
\index{Isopropyl alcohol}
You may find that during printing, printed parts lift off the print surface on the corners. If you are seeing this turning on \texttt{Brim} in Cura will help increase the surface area of the print, improving part adhesion. If the corners of the part still lift, clean the PEI surface with IPA/ Isopropyl Alcohol and sand the surface with fine grit (2000-3000) sandpaper.

\subsection{\texttt{ABS/Acetone Glue}}
\label{sec:ABS/Acetone Glue}
\index{acetone}
\index{ABS}
\index{bed adhesion}

\glossary{Acetone}{A colorless, volatile, flammable liquid ketone, (CH3)2CO, used as a solvent for ABS.}
Acetone is not included or required with the LulzBot TAZ 3D printer. \textcolor{red}{Acetone and ABS solution is NOT recommended anymore, as the PEI print surface works well without it.}

\subsection{\texttt{Glue stick/PVA Glue solution}}
\label{sec:Glue stick/PVA Glue solution}
\index{PVA}
\index{Glue stick}
\index{bed adhesion}
\index{Nylon}
\index{gluestick}
\glossary{PVA}{Polyvinyl acetate is the main ingrediant in white glue, wood glue and the common school glue stick.} While almost all 3D printing filaments will adhere well to the PEI print surface, Nylon, and Amphora\textsuperscript{\miniscule{\texttrademark}}-based print adhesion can be improved with the application of an unscented PVA glue solution/glue stick. Flexible filaments such as NinjaFlex\textsuperscript{\miniscule{\textregistered}} and SemiFlex\textsuperscript{\miniscule{\texttrademark}} can adhere too well and can be released easier from the PEI print surface with an application of an unscented PVA glue solution/glue stick to the print surface prior to starting the printing process.

%\index{PET sheet}
%\glossary{PET}{Polyethylene terephthalate.}
%To apply the acetone/ABS mixture, put a small amount onto a paper towel. Now, rub the towel onto the cool PET print surface to apply a \emph{thin} layer of ABS. Generally only one thin layer of the acetone/ABS solution is needed. However, you can apply multiple coats if needed.

\section{\texttt{Using 1.75mm filament}}
\index{1.75mm filament}
%\index{PTFE tube}
\glossary{PTFE}{Polytetrafluoroethylene is a synthetic fluoropolymer used in the Budaschnozzle for it's low coefficient of friction. This limits the Budaschnozzle top extrusion temperature to 250°C. The LulzBot TAZ 5 and TAZ 6 does not use a hot end with a PTFE insert and can reach a \texttt{300°C} extrusion temperatuere.}

Your LulzBot TAZ 3D printer is set up to use 3mm plastic filament by default and may be capable of printing 1.75mm filament with no hardware modification. While many of our advanced users are able to do so, your results may vary.  More information can be found in our User Forums at: \texttt{https://forum.lulzbot.com/viewtopic.php?f=16\&t=1923}

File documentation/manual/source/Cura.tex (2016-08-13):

%
% Cura.tex
%
% LulzBot Cura User Manual
%
% Copyright (C) 2015 Aleph Objects, Inc.
%
% This document is licensed under the Creative Commons Attribution 4.0
% International Public License (CC BY-SA 4.0) by Aleph Objects, Inc.
%

\section{\texttt{Cura}}
\index{Cura}
\label{Cura}
\glossary{\texttt{Cura}}{Cura LulzBot Edition is a cross-platform software package that combines a slicing engine with a printer host interface.}
\glossary{Slic3r}{Slic3r is a cross-platform 3D model slicing engine. It's used to process the 3 dimensional model into the GCODE (tool path) needed to physically generate the print.}
\glossary{FFF}{Fused Filament Fabrication-- the process of laying down successive layers of extruded filament to create a 3 dimensional object. As each layer of molten plastic is extruded into place, it fuses with the previous layer.}

\subsection{\texttt{Setup Cura}}
\index{Installation}
Cura LulzBot Edition is available for download on our website at \texttt{http://LulzBot.com/cura}. When installing, it is recommended to uninstall any previous versions of Cura you may have been using. Cura is designed for Fused Filament Fabrication (FFF) 3D printers. Fused Filament Fabrication is the term for the process of laying down successive layers of extruded filament to create a 3 dimensional object. As each layer of molten plastic is extruded into place, it fuses with the previous layer.
When first opening Cura, you will be prompted to go through the \texttt{First run wizard}. This will consist of selecting your printer, hot end type, tool head type, and finally your nozzle diameter.

\textcolor{red}{It is important to select the correct printer, hot end, tool head, and nozzle diameter as Cura uses custom profiles and machine settings based upon which printer, hot end, tool head, and nozzle you have.}

\begin{itemize}
\item Download the appropriate installer for your computer operating system. Instructions on installation for each operating system are available at \texttt{http://LulzBot.com/cura}.
\item Install Cura by double clicking on the installer.
\item Click through the install wizard until it completes.
\item Start Cura by launching it from your list of installed applications. If this is the first time that Cura has been used the ``Configuration Wizard'' window will open.
%\item Once your language has been selected, select \texttt{Next}.
%\item Select \texttt{LulzBot Mini}.
%\item Select \texttt{LulzBot\textsuperscript{\miniscule{\textregistered}} TAZ 4 or 5}, then select \texttt{Next}.
\item Select \texttt{LulzBot TAZ 6}. Press \texttt{Next}.
\item Select \texttt{Single Extruder v2.1}. Press \texttt{Next}
%\item The final step will be a firmware update. \textcolor{red}{Skip this step if you are not switching to different tool heads.} If you are adding on a different tool head, please be sure to update the firmware.
\item Select finish.
\end{itemize}

\section{\texttt{Quick Print Settings}}
\index{Quick Print Settings}
\begin{figure}[H]
\centering
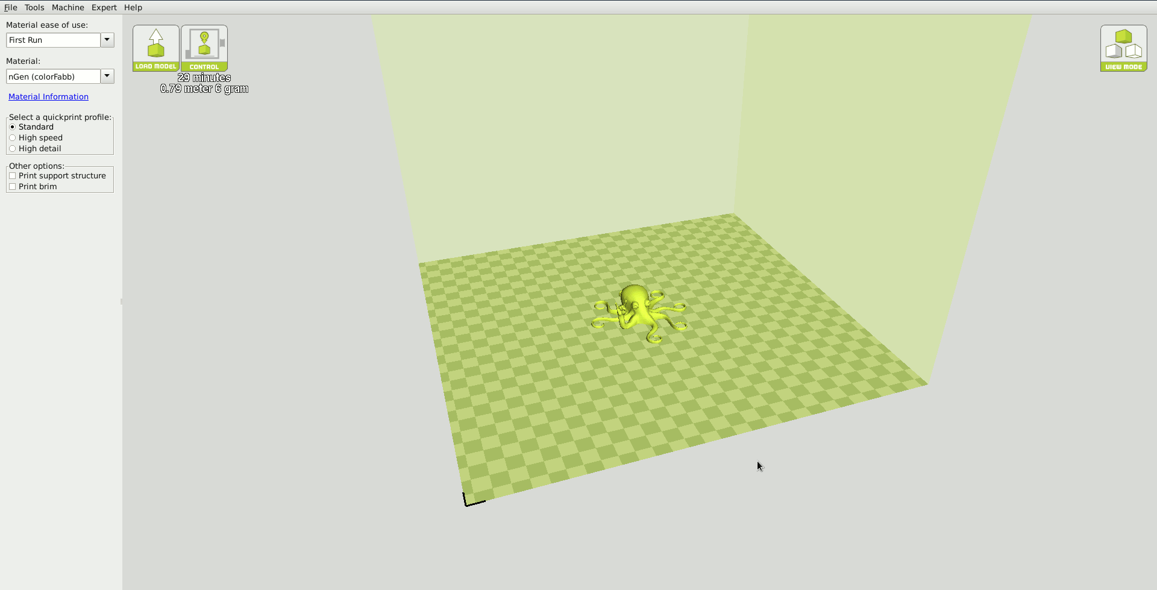
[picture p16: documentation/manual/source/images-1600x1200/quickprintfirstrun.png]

\caption{Quick Print Settings}
\label{fig:Cura}
\end{figure} 
% (photo highlighting profile, material, diameter, and other)
After setting up Cura for the first time, you will be shown the main interface screen. (Fig. \ref{fig:Cura}, page \pageref{fig:Cura}) 

\subsection{\texttt{Selecting a Quick Print Profile}}
\index{Quick Print Profile}
\index{Resolution}
\glossary{Resolution}{In general terms, the resolution you print at can be determined by the layer height you use. The LulzBot TAZ can print at a layer height of 0.05mm to 0.50mm.}
The print quality settings can be found in the top left-hand corner of the window. For most filaments, there will be \texttt{Standard}, \texttt{High Speed}, and \texttt{High Detail} options. Some of the more exotic filaments may only have a single profile.

\begin{description}
\item[\texttt{High Detail}] \hfill \\
Designed to give greater detail and finer objects. This will have a smaller layer height, which will make each layer thinner, so that curves seem more natural and walls seem less noticeable. This setting will also require more layers to be laid down, increasing overall print time.
\index{High Detail}

\item[\texttt{Standard}] \hfill \\
Designed to give a balanced resolution by increasing the layer height and print speeds. This will make the organic curves slightly more step-like than the fine setting, but it will reduce printing time.
\index{Standard Quality}

\item[\texttt{High Speed}] \hfill \\
Designed for the fast prints, where the overall model finish is not of concern. Most commonly used for quick iteration of designs when rapid prototyping.
\index{High Speed}
\end{description}

\subsection{\texttt{Material Selection}}
\index{Material Selection}
\index{filament}
We have the different filaments separated by \texttt{Material ease of use.} From the \texttt{Material ease of use} drop down, select \texttt{"All"} to view all our pre-loaded filament slicing profiles. The TAZ ships with a filament sample for the first print. Refer to the included Quick Start Guide for the proper ``First Run'' settings.
%If you are not using LulzBot supplied filament, update your filament diameter to your specific average filament diameter. Do this by taking 10 to 12 filament diameter measurements from different parts of the reel and averaging them. Update your filament diameter. You may also want to adjust the temperature, as different manufacturers have different recommended temperatures. % This could be better served in the Full Settings explanation.

\subsection{\texttt{Printing Support Material}}
\index{Support Material}
%%%% Saved for standalone Cura Manual %%%%
%The TAZ and Mini are able to print models that have angles and overhangs, even without support material depending on the overhang distance and angle. Turn this option on if your model could benefit from support material.
%MINI% The Mini 3D printer is able to print models that have angles and overhangs, even without support material depending on the overhang distance and angle. Turn this option on if your model could benefit from support material.
The LulzBot TAZ 3D printer is able to print models that have angles and overhangs, even without support material. This will depend on the overhang distance and angle of your particular model file. Turn this option on if your model could benefit from support material.

\subsection{\texttt{Brim}}
\index{Brim}
Brim is used to increase surface area of the part you're printing, thereby ensuring proper part adhesion. This will print a single layer high edge around the base of the part, helping first layer adhesion and minimizing warping.

\subsection{\texttt{Load Model File}}
\index{Load Model}
\index{STL}
Select the STL model you would like to print. Either use the \texttt{Load Model} button or select \texttt{File} > \texttt{Load Model}. Once the file has been loaded, you will see a 3D rendering of your object on the build platform. Select the model to see the various options. 

\subsection{\texttt{Model Orientation}}
\index{Orientation}
Move your model to change where it is printed on the build plate. Do this by left clicking on the model and dragging it to the desired location. The \texttt{black} outlined corner of the 3D print bed view represents the front left hand corner of the build plate on your printer. By holding down the right mouse button and dragging, you can view your model from different angles. %Not sure if this last sentence should be reworked or put in a separate section.
\begin{figure}[H]
\centering
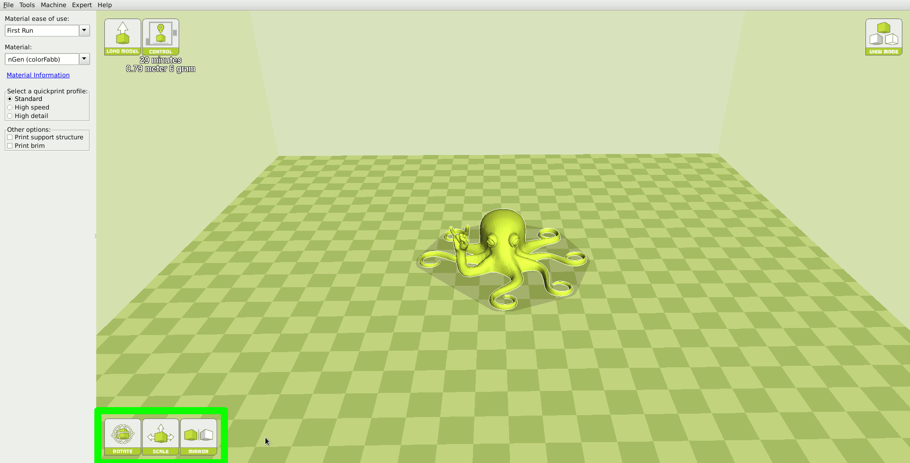
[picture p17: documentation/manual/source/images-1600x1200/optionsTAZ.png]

\caption{Options after selecting model}
\label{fig:Orientation}
\end{figure}

\subsubsection{\texttt{Rotate}}
\index{Rotating Object}
%%%% Alternate explanation %%%%
%The \texttt{Rotate} button will give you the ability orient your model in along all three axes. Once you click the rotate button, three circles will surround your model. The red circle will allow you to rotate in the XY plane. The Yellow circle will rotate in the XZ plane. The Green circle will rotate in the YZ plane.
\definecolor{yellow1}{cmyk}{0,0,1,0.30}
\definecolor{green1}{rgb}{0.30,1,0.30}
The \texttt{Rotate} button will give you the ability to orient your model in along all three axes. Once you click the rotate button, three circles will surround your model. The \textcolor{red}{red circle} will allow you to rotate around the \textcolor{red}{Z-axis}. The \textcolor{yellow1}{Yellow circle} will rotate around the \textcolor{yellow1}{Y-axis}. The \textcolor{green}{Green circle} will rotate around the \textcolor{green}{X-axis}. Cura defaults to 15 degree increments. Hold \texttt{Shift} to rotate by \texttt{One Degree Increments}.
\begin{figure}[H]
\centering
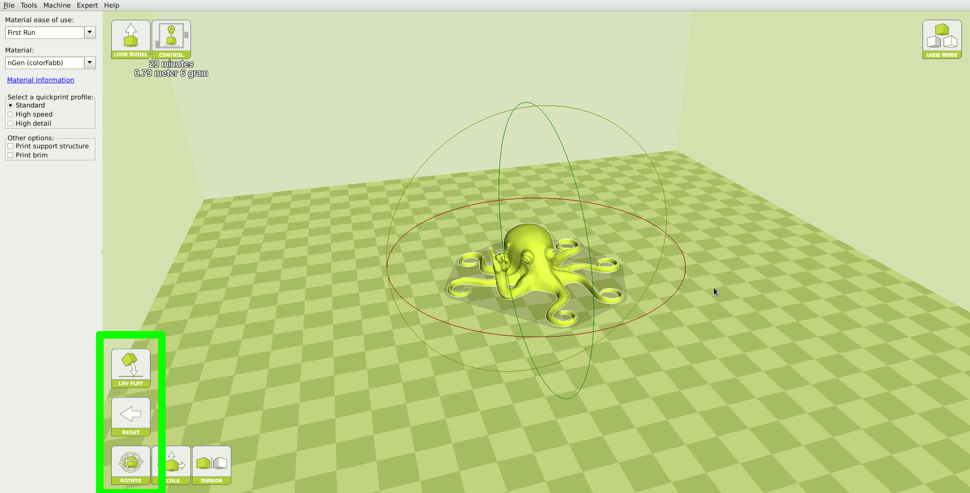
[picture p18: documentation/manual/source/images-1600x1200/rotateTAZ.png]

\caption{Rotating your Model}
\label{fig:Rotating your Model}
\end{figure}

\subsubsection{\texttt{Lay Flat}}
The \texttt{Lay Flat} button will ensure that the flat portion of your print is securely attached to the bed. It is highly recommended to use this option after rotating your model in the Z direction, as it will help prevent potential adhesion issues during the print.
%\begin{figure}[hbt]
%\centering
%\includegraphics[keepaspectratio=true,angle=0,height=0.4\textheight,width=1.0\textwidth]{Rotate.png}
%\caption{Rotating your Model}
%\label{fig:Rotating your Model}
%\end{figure}

\subsubsection{\texttt{Reset}}
The \texttt{Reset} button will return your model to the original orientation as defined by the CAD program used to create the model.
%\begin{figure}[hbt]
%\centering
%\includegraphics[keepaspectratio=true,angle=0,height=0.4\textheight,width=1.0\textwidth]{Rotate.png}
%\caption{Rotating your Model}
%\label{fig:Rotating your Model}
%\end{figure}

\subsubsection{\texttt{Scale}}
The \texttt{Scale} button displays the model dimensions, along with the ability to scale along the X Y or Z axes. Anything \texttt{below} the number \texttt{1.0} will reduce the objects size, while anything \texttt{above} the number \texttt{1.0} will increase the objects size. As a default, it will be set to uniform scaling. This will cause the X Y and Z axes to be scaled by the same amount when you make a change to any of them. To disable this, select the lock in the lower section of the scaling window. 
\begin{figure}[H]
\centering
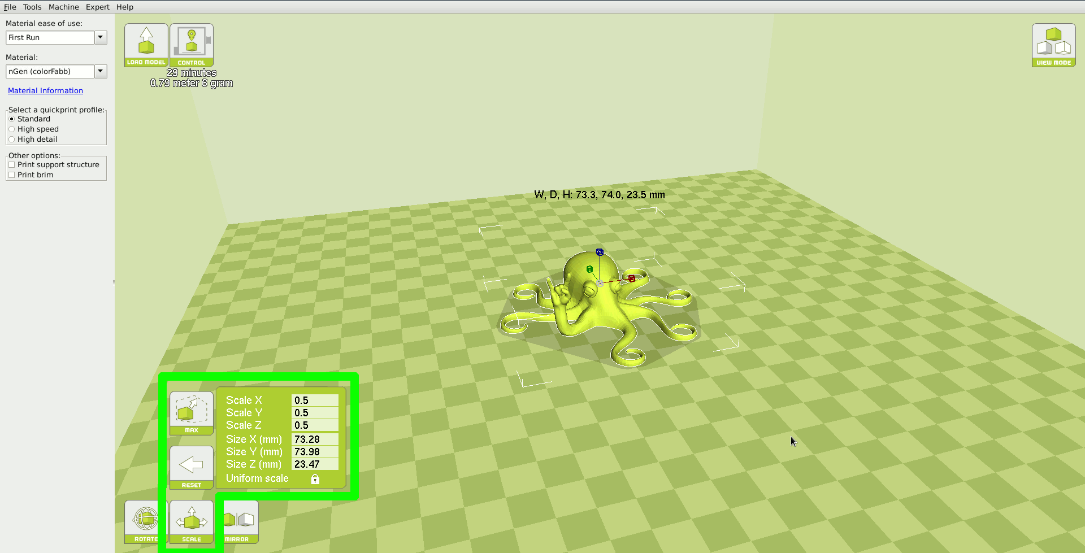
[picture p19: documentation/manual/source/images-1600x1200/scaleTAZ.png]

\caption{Scaling your Model}
\label{fig:Scaling your Model}
\end{figure}

\section{\texttt{View Options}}
\index{View Options}
Different modes allow you to view your model in a variety of ways. This can be helpful for spotting issues before the print even starts. 

\subsection{\texttt{Normal}}
\index{Normal View}
This is the standard view and shows the solid outer surfaces of the model. (Fig. \ref{fig:Normal View}, page \pageref{fig:Normal View}): 

\begin{figure}[H]
\centering
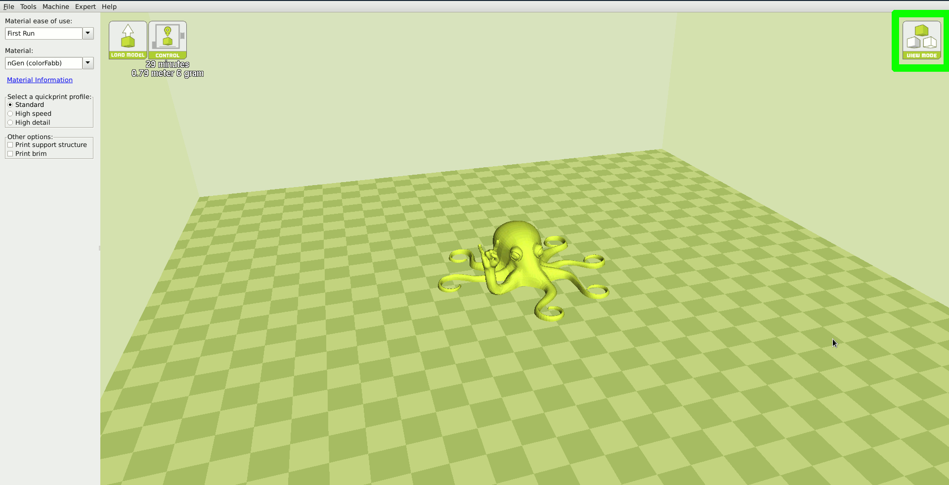
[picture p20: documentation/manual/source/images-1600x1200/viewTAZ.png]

\caption{View in Normal Mode}
\label{fig:Normal View}
\end{figure}

\subsection{\texttt{Overhang}}
\index{Overhang View} 
Overhang mode shows where your model may need support material. In Fig. \ref{fig:Overhang_View}, page \pageref{fig:Overhang_View} the red highlighted areas show overhangs and more severe angles and areas where support material is recommended. The overhang threshold can be defined in Expert Settings.
\begin{figure}[H]
\centering
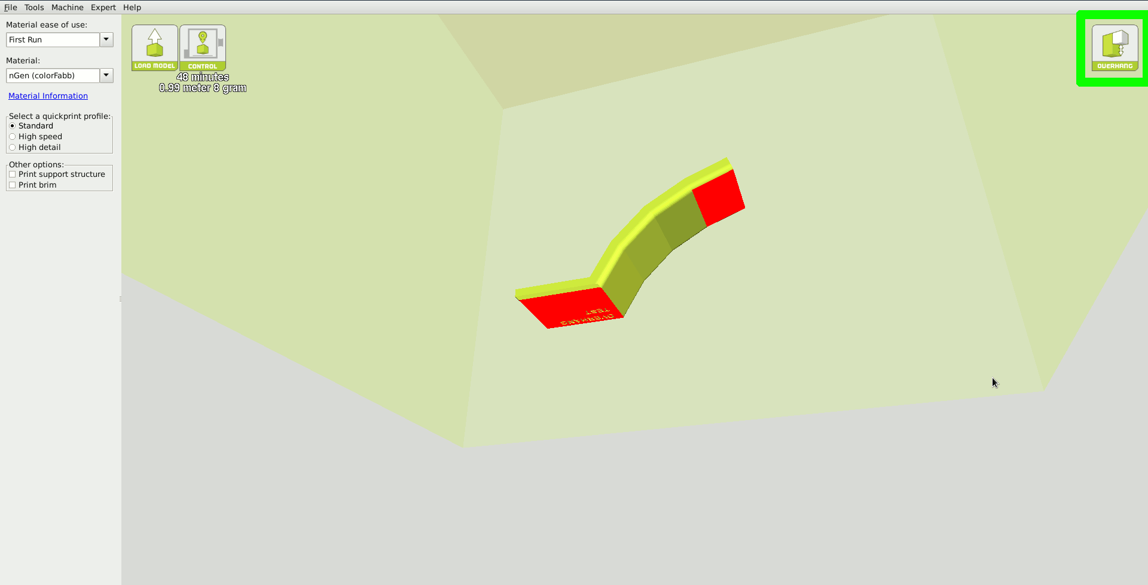
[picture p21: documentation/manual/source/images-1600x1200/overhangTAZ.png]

\caption{View in Overhang}
\label{fig:Overhang_View}
\end{figure}

\subsection{\texttt{Ghost}}
\index{Ghost View}
Ghost view mode makes the model translucent to allow you to see what is behind it.
\begin{figure}[H]
\centering
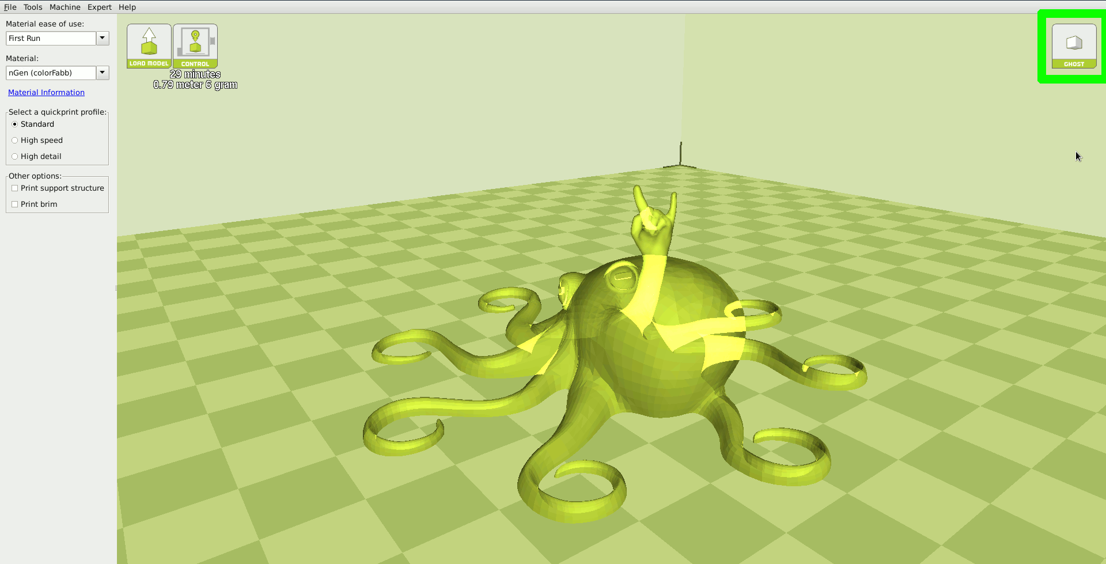
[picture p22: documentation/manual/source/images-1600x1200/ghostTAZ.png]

\caption{View in Ghost}
\label{fig:Ghost View}
\end{figure}

\subsection{\texttt{Xray}}
\index{Xray}
Xray is similar to Ghost mode. It will allow you to see into objects, ensuring that inner details are correct.
\begin{figure}[H]
\centering
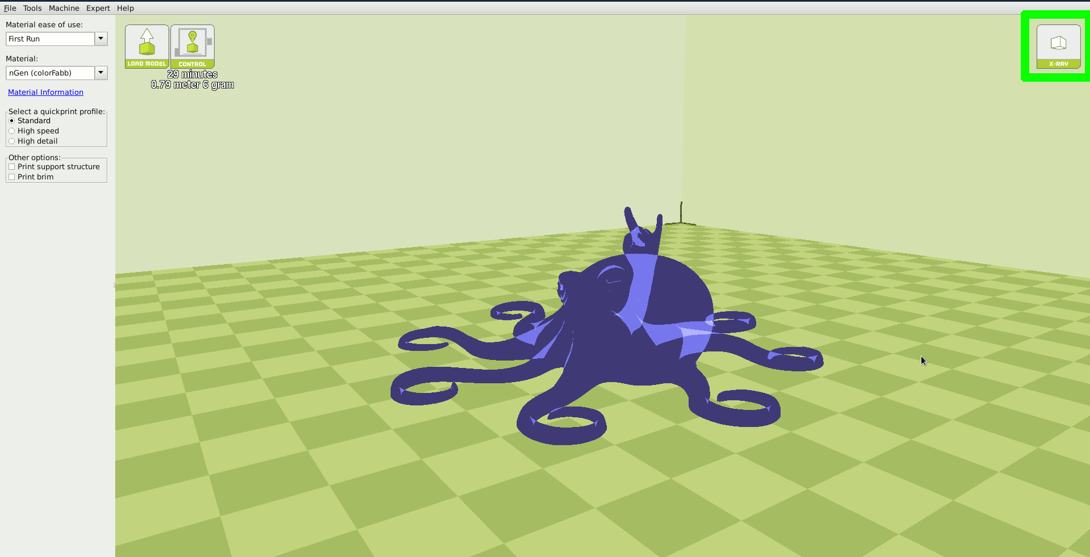
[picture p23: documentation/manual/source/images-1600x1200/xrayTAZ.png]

\caption{View in Xray}
\label{fig:Xray View}
\end{figure}

\subsection{\texttt{Layers}}
\index{Layers View}
To view the tool path of your print head and to ensure no skipped layers or gaps use this option. Use the slide bar on the right hand side of the window to move up and down through the tool path layers. Click the icon below it to view an individual layer at a time. If the \texttt{Print support structure} option is activated in Cura, it will be shown in blue.
\begin{figure}[H]
\centering
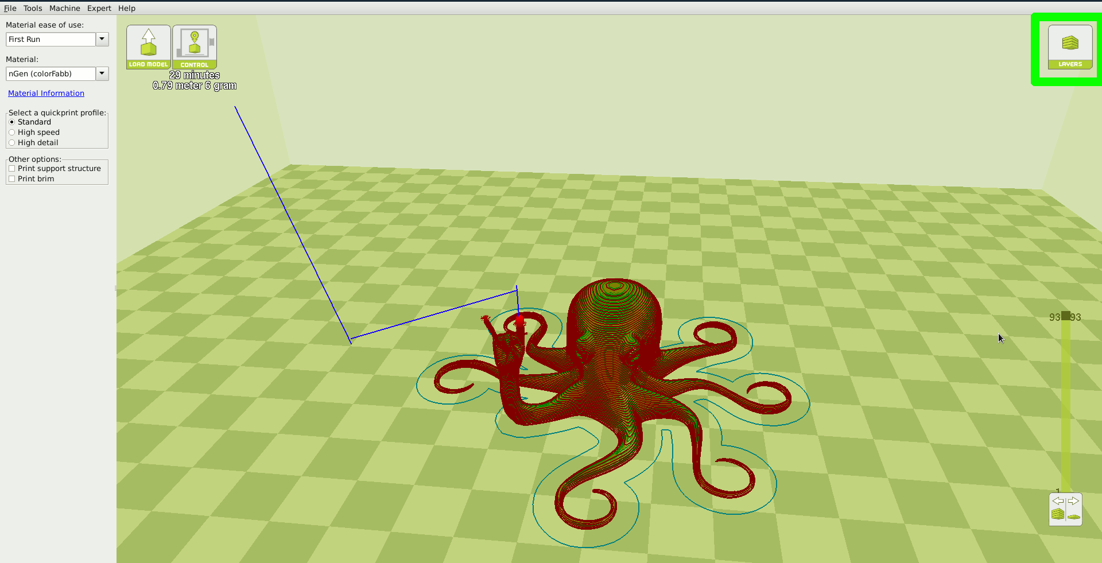
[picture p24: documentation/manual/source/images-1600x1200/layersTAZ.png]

\caption{View in Layers}
\label{fig:Layers View}
\end{figure}

\begin{figure}[H]
\centering
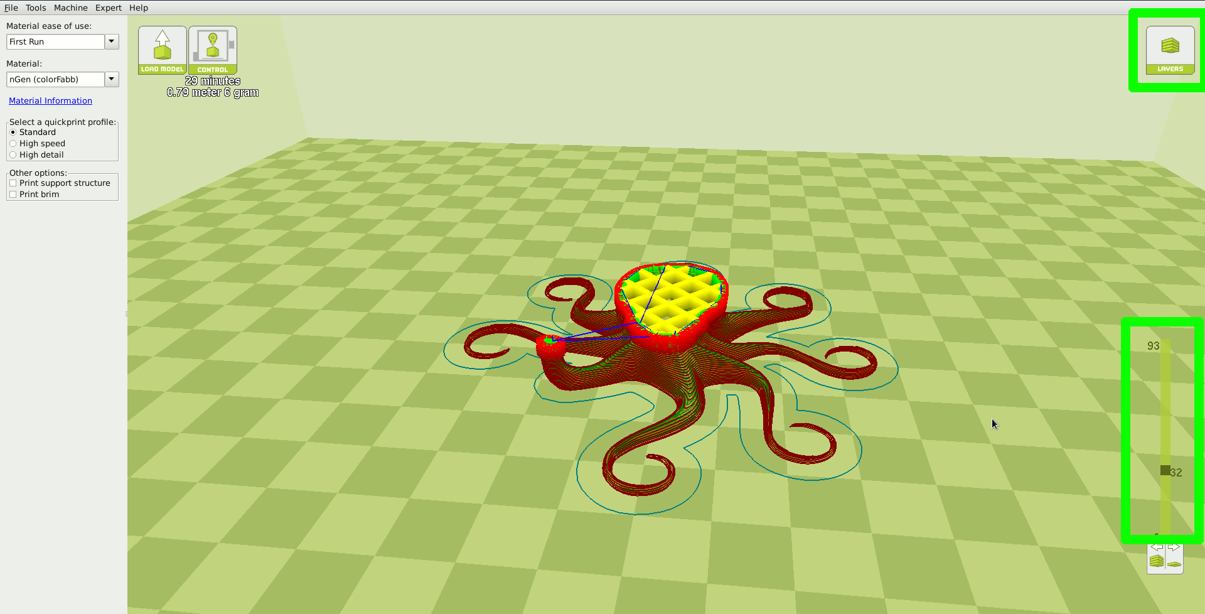
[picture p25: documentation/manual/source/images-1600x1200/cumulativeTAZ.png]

\caption{Viewing Cumulative Layers}
\label{fig:Mid Layers View}
\end{figure}

\begin{figure}[H]
\centering
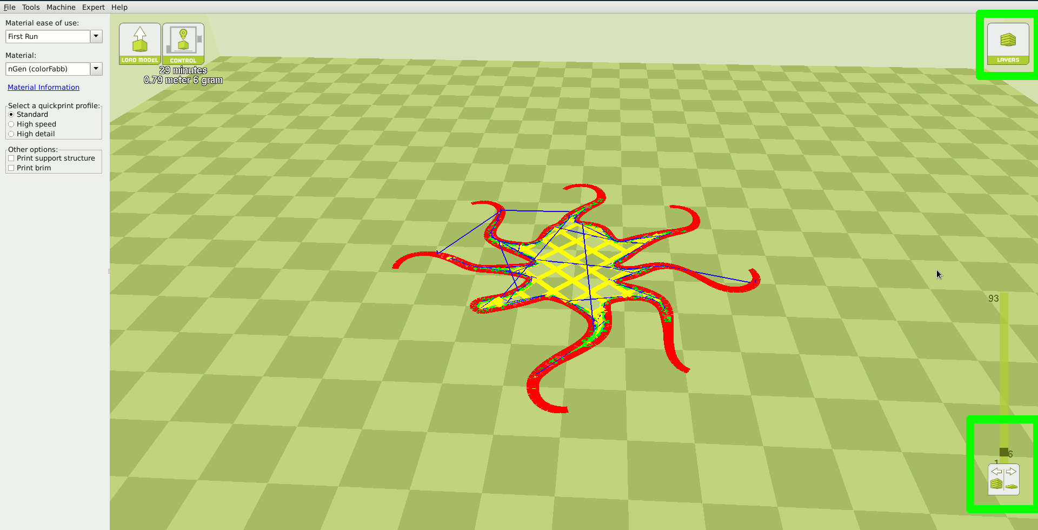
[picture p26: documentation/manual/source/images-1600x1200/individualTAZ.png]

\caption{Viewing Specific Layers}
\label{fig:Viewing Specific Layer}
\end{figure}

\section{\texttt{Starting Your First Print}}
\index{First Print}
Once you have your model, profile, and filament loaded, it is time for your first print! Refer to the \texttt{Quick Start Guide} included with your 3D printer. A PDF version is available at \texttt{LulzBot.com/downloads}.

\subsection{\texttt{Automatic Bed Leveling}}
\index{Automatic Bed Leveling}
\index{ABL}
Before each print your, TAZ will go through a wiping and a probing procedure in order to determine the slope/tilt of your bed. If your nozzle is dirty or not cleaned properly, this will prevent the printer from being able to create an electrical contact with the corners. Your TAZ will automatically retry the wiping and probing procedure if this happens, up to a maximum of three times. If three consecutive wipes and probes have failed, the printer will stop and a warning will sound. If this is happening consistently, you should replace the wiping pad and/or adjust your wiping and probing temps for that specific filament. See section \ref{sssec:num1} on page \pageref{sssec:num1} for details on changing these temps.
%\subsection{Mini}

%Select the \texttt{Print/Control} option in the top left hand corner of your build volume. This will bring up your Printer Interface. Please wait for the window title to display \texttt{operational} before sending any commands to the printer..

%\pageref{fig:Print Control}).
%\begin{figure}[hbt]
%\centering
%\includegraphics[keepaspectratio=true,angle=0,height=0.4\textheight,width=1.0\textwidth]{print_control.png}
%\caption{Print Control Screen}
%\label{fig:Print Control}
%\end{figure}

%\subsection{TAZ}

%Your TAZ 3D printer has the ability to print directly from a computer using the included USB cable, or directly from the SD card by using the Graphical LCD controller.

%%%% SD Printing %%%%
\subsection{\texttt{Printing from SD Card}}
\index{Printing from SD}
\index{Graphical LCD controller}
\index{GLCD}
\index{SD card}
\index{SD}

Load your model into Cura with the proper filament and profile selected. Next, insert the included SD card into your computer. Select \texttt{File} > \texttt{Save GCODE} and choose the SD card location to save your GCODE file to your SD card. Safely eject the card from the computer, and insert it into the Graphical LCD Controller. 

%\subsection{\texttt{Set Temperature}}

%Turn on the heated bed and hot end by using the Graphical LCD controller and navigating to: \texttt{Temperature} > \texttt{Select Filament type}. If you are using other than a preset material, you can set your desired temperatures by going to \texttt{Temperature} > \texttt{Custom Temp} > \texttt{Nozzle/Bed}. Wait for your 3D printer to reach specified temperatures.

\subsection{\texttt{Start Print}}
\index{printing}
Thanks to the TAZ automatic bed leveling system, it is now time to kick off the print! Through the LCD screen go to: \texttt{Print From SD} > \texttt{Desired File}. Your TAZ will then go through it's automatic cleaning and wiping process before starting the print. This should take approximately 5 minutes.

%%%% Tethered printing %%%%

\subsection{\texttt{Printing from USB Cable}}
\index{Printing from USB}

Connect your 3D printer to a computer using a USB cable, power it on and select the \texttt{Control} button at the top of the 3D viewing window. If the control button is not present, be sure you have a model file loaded into Cura. If a model is loaded but the Control button is still not present use a different USB cable, reinstall Cura, or contact our Support Team. This will bring up your Printer Interface. You will not be able to send any commands until the window title changes to \texttt{Operational}. Once operational, you can start your first print. Your TAZ will then go through it's automatic cleaning and wiping process before starting the print. This should take approximately 5 minutes.

\begin{figure}[H]
\centering
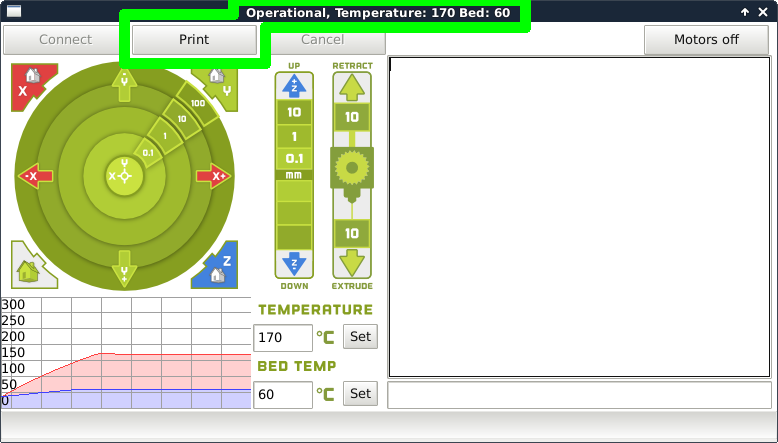
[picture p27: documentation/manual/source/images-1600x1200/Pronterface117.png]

\caption{Control Screen}
\label{fig:Control}
\end{figure}

\subsection{\texttt{Pausing Mid-Print}}
\index{Pause}
You will notice after you click the print button through Cura, it will change to a pause button. When activated, it will pause the print and automatically move your print head away from your object. This will allow color changes or material changes mid print.

\subsection{\texttt{Recommended Temperatures and Bed Preperation}}
\index{Temperatures}
\index{Glue stick}
When generating GCODE, it may be beneficial to adjust temperatures depending on your specific model file or filament. We have also found that for certain materials applying unscented glue stick to the print surface is required for successful bed adhesion and/or part release. Glue stick can also be added to help first layer adhesion on any material, and may be helpful for objects with a larger surface area. You can find our recommended temperature ranges and adhesion techniques below.

\begin{table}[H]
	\begin{center}
 		\hspace*{-1.5cm}\begin{tabular}{||c c c c c||} 
 		\hline
 		Filament Type & Bed Preparation & Nozzle Temp & Bed Temp & Removal Temp \\ [0.5ex] 
 		\hline\hline
 		ABS & Clean PEI & 230-250 & 110 & 50 \\ 
 		\hline
 		PLA & Clean PEI & 195-215 & 60 & 45\\
 		\hline
 		HIPS & Clean PEI & 230-250 & 110 & 50 \\
 		\hline
 		Laywoo-D3 & Clean PEI & 175-195 & 60 & 45 \\
 		\hline
		bambooFill & Clean PEI & 185-195 & 60 & 50 \\ 
 		\hline
		woodFill & Clean PEI & 185-195 & 60 & 50 \\
 		\hline
 		Laybrick & Clean PEI & 175-195 & 60 & 45 \\
		\hline
		bronzeFill & Clean PEI & 225-235 & 60 & 50 \\
		\hline
		copperFill & Clean PEI & 225-235 & 60 & 50 \\
 		\hline 
 		Magnetic Iron PLA & Clean PEI & 220-230 & 60 & 50 \\
 		\hline
 		Stainless Steel PLA & Clean PEI & 220-230 & 60 & 50 \\
 		\hline
 		Conductive PLA & Clean PEI & 215-230 & 60 & 50 \\
		\hline
		Coffee PLA & Clean PEI & 220-230 & 60 & 40 \\
 		\hline
 		nGen & Clean PEI & 220-240 & 85 & 60 \\
 		\hline
 		t-glase & Glue stick & 240-260 & 60 & 45 \\
 		\hline
 		Flexible Filaments & Glue stick & 215-230 & 50 & 35 \\  
 		\hline
 		Nylons & Glue stick & 220-270 & 110 & 50 \\
 		\hline
 		Polycarbonate & Glue stick & 260-300 & 110 & 50 \\ 
 		\hline
 		Polycarbonate + ABS & Glue stick & 260-280 & 110 & 50 \\
 		\hline
 		INOVA 1800 & Glue stick & 235-255 & 75 & 50 \\
 		\hline
 		n-vent & Glue stick & 225-245 & 60 & 50 \\ [1ex]
 		\hline
 
		\end{tabular}
		\caption{Recommended Temperatures}\label{tab:a}
	\end{center}
\end{table}
%%mini:
%This will start the printing process: (set the appropriate temperatures, go through the automatic bed leveling procedure, and start printing your model).
%\pageref{fig:Print Control}).

\section{\texttt{Removing Your First Print}}
\index{Removing a Print}
After your first print has finished, wait for the print surface to cool to the recommended print removal temperature.  Your parts will be easier to remove if you allow your heated bed to cool down to optimal temperature. This will allow the plastic to contract, making it easier to remove. 
%\texttt{Your print bed will move forward once it is ready to be removed.}

Once your heated bed has cooled, use the blue handled knife that was included with your toolkit to remove the item. Carefully insert the blade of the knife between your print and heated bed. Once underneath the part rotate the blade lifting with the sharp edge into the part, to gently pop the piece off your plate.
%\begin{figure}[hbt]
%\centering
%\includegraphics[keepaspectratio=true,angle=0,height=0.4\textheight,width=1.0\textwidth]{remove_part.png} %%%% Photo needed %%%%
%\caption{Remove Part}
%\label{fig:Remove part}
%\end{figure}

\section{\texttt{Full Settings}}
\index{Full Settings}
\textcolor{red}{Full settings should not be used until enough experience with 3D printing has been gained to feel comfortable with all aspects of the printer and its operation.} Quickprint Mode will provide good results for most models.
The first time Cura is launched it will default to the \texttt{Quick Print} interface. In order to have more control of your slicing and GCODE generation, switch to \texttt{Full Settings}. Choose your desired Quick Print profile, as you can copy over the current settings when changing to \texttt{Full Settings} mode. This will automatically update the settings for that filament. Select \texttt{Expert} > \texttt{Switch to Full Settings}. The following tabs will now be available: Basic, Advanced, Plugins, and Start/End-GCODE. You will also have access to the Expert Settings menu entry. 
\begin{figure}[H]
\centering
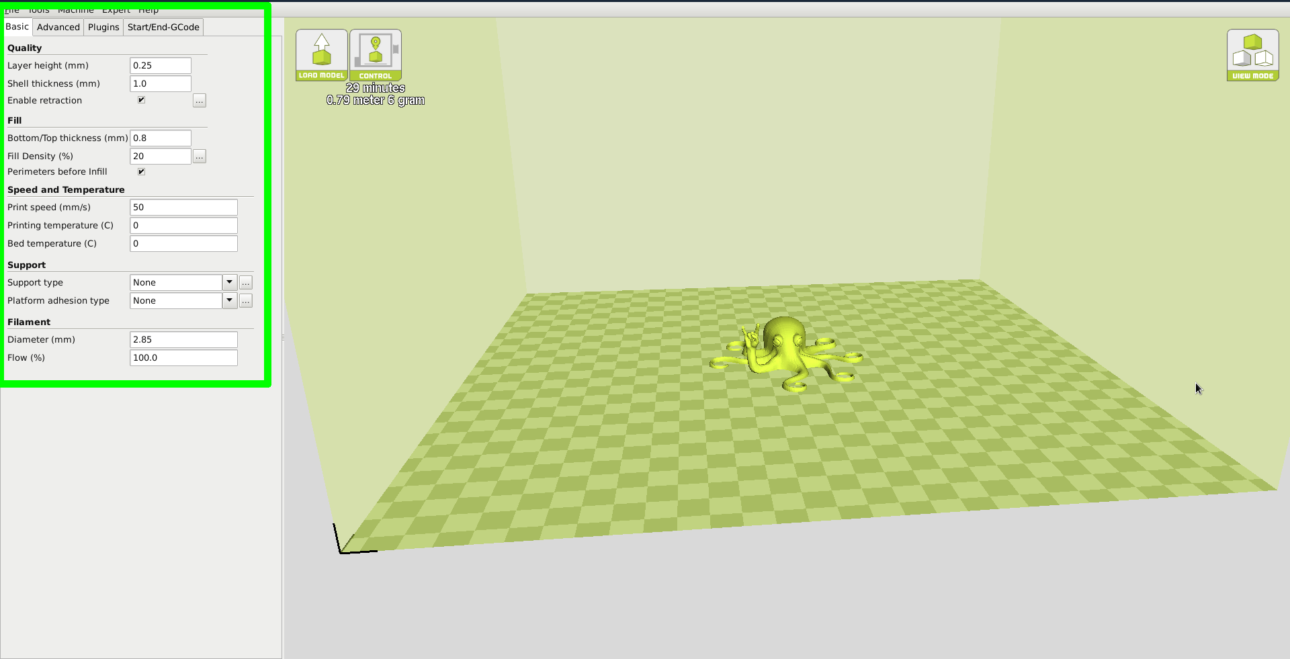
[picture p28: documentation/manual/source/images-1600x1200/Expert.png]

\caption{View in Full Settings}
\label{fig:Full Settings View}
\end{figure}

%\subsection{View in Full Settings}
%\index{Full Settings}
%When you first switch to Full Settings, Cura will need to know what filament and quality you wish to use. It will automatically transfer our quickprint settings over to allow adjustments if one is selected. \textcolor{red}{IF A QUICKPRINT PROFILE IS NOT AVAILABLE, YOU WILL NEED TO MANUALLY LOAD ONE IN.} We recommend using our tested profiles that are available here: \texttt{https://www.lulzbot.com/cura}. You will want to choose the profile that matches your filament and quality needs. Once downloaded, you can load the file into Cura by selecting \texttt{File} > \texttt{Open Profile}. Choose your desired profile. This will automatically update all of your settings for use with your printer.
%\begin{figure}[hbt]
%\centering
%\includegraphics[keepaspectratio=true,angle=0,height=0.4\textheight,width=1.0\textwidth]{Expert.png}
%\caption{Full Setting Options}
%\label{fig:Expert Options}
%\end{figure}

\subsection{\texttt{View in Full Settings}}
\index{Full Settings}
When you first switch to Full Settings, Cura will need to know what filament and quality you wish to use. It will automatically transfer our quickprint settings over to allow adjustments if one is selected. \textcolor{red}{IF A QUICKPRINT PROFILE IS NOT AVAILABLE, YOU WILL NEED TO MANUALLY LOAD ONE IN.} We recommend using our tested profiles that are available here: \texttt{https://www.lulzbot.com/cura}. You will want to choose the profile that matches your filament and quality needs. Once downloaded, you can load the file into Cura by selecting \texttt{File} > \texttt{Open Profile}. This will automatically update all of your Cura settings for use with your specific filament.
%\begin{figure}[hbt]
%\centering
%\includegraphics[keepaspectratio=true,angle=0,height=0.4\textheight,width=1.0\textwidth]{Expert.png}
%\caption{View in Full Settings}
%\label{fig:Full Settings View}
%\end{figure}

\section{\texttt{Basic Tab Options}}
\index{Basic Options}

\subsubsection{\texttt{Layer Height}}
\index{Layer Height}
The thickness of each printed layer is known as the ``Layer Height''. The smaller the layer height, the smoother curves will appear. Larger layer heights are better for bridging and overhangs. Smaller layer heights will also increase print time, as it will take more layers to complete the object.
% (Layer height comparison photos)
\begin{figure}[H]
\centering
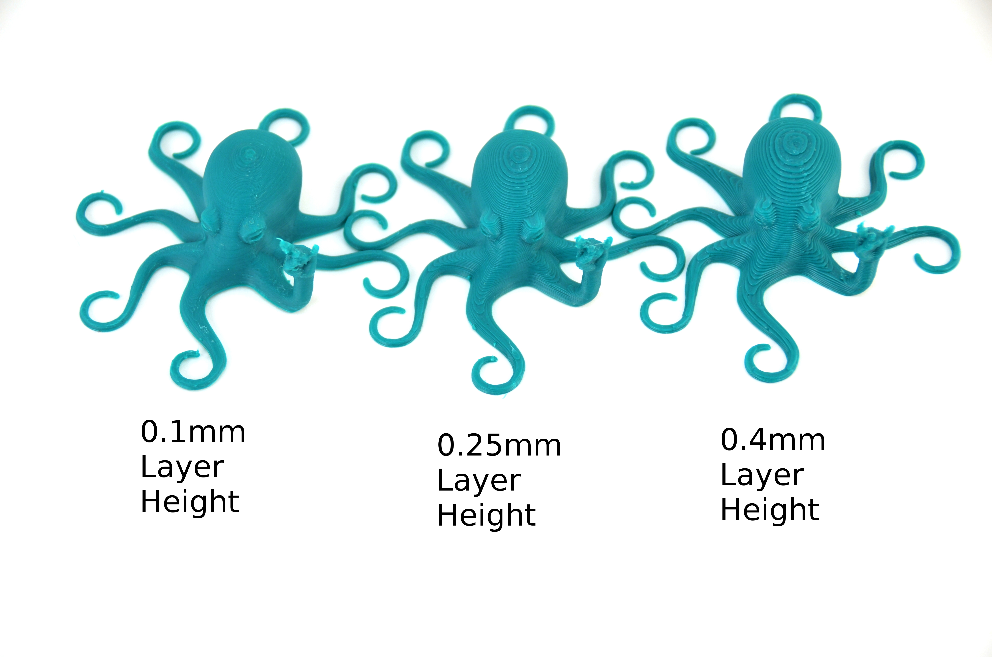
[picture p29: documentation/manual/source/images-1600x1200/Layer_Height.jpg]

\caption{Differences in Layer Height}
\label{fig:Differences in Layer Height}
\end{figure}

\subsubsection{\texttt{Shell Thickness}}
\index{Shell Thickness}
This defines the number of vertical walls that comprise the outside of your model. We recommend keeping this set to multiples of your nozzle width. Your TAZ 3D printer is equipped with a 0.5mm nozzle. %The TAZ ships with a .5mm nozzle standard, while the Mini has a .5mm nozzle standard.

\subsubsection{\texttt{Enable Retraction}}
\index{Retraction}
Retraction tells your printer to pull filament out of the hot end upon travel moves. Travel moves are when your print head moves from one area of the print, to another without laying down filament. We recommend keeping this on for all filament types, and adjusting the retraction length and speed for the specific filament.
%(Details given in advanced tab section. ((Reference?))

\subsubsection{\texttt{Bottom/Top Thickness (mm)}}
\index{Bottom Thickness}
\index{Top Thickness}
Also known as ``Surface Layers'' this will determine how thick the top and bottom layers are. A larger number here will create a thicker top and bottom which can be helpful for strength, bridging, and quality purposes. We recommend keeping this number as a multiple of your layer height.

\subsubsection{\texttt{Fill Density}}
\index{Fill Density}
This number is expressed as a percentage. 0\% will give a completely hollow print, while 100\% will give you a completely solid object. We have found that 20\% to 40\% fill density is functional for most prints.

\subsubsection{\texttt{Perimeters Before Infill}}
This option will toggle the order in which the infill and perimeters will be printed. We recommend leaving this on.
\subsubsection{\texttt{Print Speed (mm/s)}}
\index{Print Speed}
Your overall printing speed can be adjusted here. If no other speeds are determined in the later sections your printer will automatically default to this speed. This speed will be different, depending on what type of filament you are using.

\subsubsection{\texttt{Printing Temperature}}
\index{Printing Temperature}
This is where you will set the hot end temperature for your specific material. It will be preset when using the recommended quickprint profiles. This can be adjusted for fine tuning of different filament manufacturers to help layer adhesion or stringing. See Recommended Temperatures Table: page \pageref{tab:a}. Your hot end is capable of reaching a maximum temperature of \texttt{300°C}.

%The Mini 3D printer needs to have the temperature specified in order to run through the automatic bed leveling routine.
%%%% Since the Mini needs to have GCODE temps set in order to run through automatic bed leveling, the following statement is only applicable to the TAZ 4 or earlier. %%%%
%We recommend leaving this temperature setting to “0”. If you set your temperature in this section your printer will not begin printing until it reaches the EXACT temperature. We recommend setting your printing temperatures through the Printer Interface, or through your LCD.

\subsubsection{\texttt{Bed Temperature}}
\index{Bed Temperature}
This is where you will set the print surface temperature for your specific material. These will be preset when using the recommended quickprint profiles. This can be adjusted for fine tuning of different filament manufacturers to help adhesion or release. See Recommended Temperatures Table: page \pageref{tab:a}. Your print surface is capable of reaching a maximum temperature of \texttt{125°C}. 

\subsection{\texttt{Support Type}}
\index{Support Type}
Some models will require support material in order to print properly. This will usually occur when an object has an angle in relation to the build plate between 0 to 45 degrees. It is highly recommended to orient your object so that it minimizes or eliminates the need for support.

\subsubsection{\texttt{Touching Buildplate}}
This causes the support material to build up between the heated bed and the object. The red example is Touching Buildplate.
% (Photo of Circle inside a square, that is printed vertically. Have samples on photo table. Reference photo below?)

\subsubsection{\texttt{Everywhere}}
This prints support material between the heated bed and object as well as between the object and itself. The green example is Support Everywhere.
% (Photo of Circle inside a square, that is printed vertically, sample on photo table. Reference Photo Below?)
% (Support Comparison Photo)
\begin{figure}[H]
\centering

\caption{Support Types}
\label{fig:Different Types of Support}
\end{figure}

\subsection{\texttt{Platform Adhesion Type}}
\index{Adhesion Type}
Some models have a small surface area contacting the plate. This can create adhesion issues causing your part to pop off at some point during the print. To fix this, use either \texttt{Brim} or \texttt{Raft}. Raft is better used when a model has small heated bed contact points and overhangs.

\subsubsection{\texttt{Brim}}
\index{Brim}
Brim will create a single layer of filament, contacting and surrounding your model. This will increase the surface area of the part contacting the build platform thereby preventing it from popping off the heated bed. Brim will also help in situations where you are seeing corner lift. Brim settings can be adjusted in the \texttt{Expert Settings} options.
% (See Expert Settings/Page REFERENCE)

\subsubsection{\texttt{Raft}}
\index{Raft}
%% Raft is rarely used these days %%
Raft will generate a layer of material underneath your object. Raft was more often used before the addition of heated plates to increase surface area. Raft settings can be adjusted in the \texttt{Expert Settings} options.

\subsection{\texttt{Filament Diameter}}
\index{Filament Diameter}
The filament diameter setting is one of the more important settings. Make sure that you update this value periodically with your average filament diameter. While your filament may be referred to as 3mm, it is more likely going to be near 2.9mm +/- 0.1mm. You will want this to be an accurate average, as it will allow your printer to correctly calculate how much filament it is pulling into the hot end. The default value should be set to 2.85mm.

\subsection{\texttt{Filament Flow \%}}
\index{Flow Rate}
This controls how much filament your printer is extruding in relation to speed. This setting is mainly used to adjust for filament density variations. This may need to be adjusted when switching between different manufacturers or types of filament to adjust for die swell. It is recommended to make small adjustments between prints for fine tuning.

\section{\texttt{Advanced Tab Options}}
\index{Advanced Options}

\subsection{\texttt{Nozzle Size (mm)}}
\index{Nozzle Size}
%%%% standalone version line %%%%
This defines your nozzle size. The slicing engine uses this value combined with your other settings to determine how quickly to feed filament into your hot end. The TAZ ships with a 0.5mm nozzle standard. 

%This defines your nozzle size. The slicing engine uses this value combined with your other settings to determine how quickly to feed filament into your hot end. The Mini ships with a 0.5mm nozzle.

\subsection{\texttt{Retraction Speed (mm/s)}}
\index{Retraction Speed}
Retraction Speed determines the speed at which your filament is reversed out of the hot end for travel moves and when changing direction during printing. We recommend keeping this set to less than 25mm/s to help protect the gears.

\subsection{\texttt{Retraction Distance}}
\index{Retraction Distance}
Retraction Distance determines how much filament is pulled out of your hot end on travel moves and when changing direction. You will want to adjust this depending on temperature settings and filament type. Higher thermal retaining filaments such as PLA behave better with a longer retraction distance. We have found anywhere from 1mm to 3mm is a good starting range.
% changed from "1 to 6mm" to remain conservative.

\subsection{\texttt{Initial Layer Thickness}}
\index{Initial Layer}
This will control how thick your first printed layer height is printed onto the heated bed. A larger initial layer height is more forgiving and will help first layer adhesion. All of our standard profiles have a 0.425mm initial layer height. This eliminates the need for adjustments when switching between filaments.  \textcolor{red}{Your LulzBot TAZ automatic bed leveling system could be affected if you change this from the standard profiles. Adjust at your own risk.}
\subsection{\texttt{Initial Layer Line Width}}
\index{Initial Layer Width}
This will control how wide your first extruded filament path is for the initial layer. A wider line width will help with bed adhesion. We have found 125\% to be a good starting place. For models with moving, printed in place parts, a smaller initial layer line width is recommended. \textcolor{red}{Your LulzBot TAZ automatic bed leveling system could be affected if you change this from the standard profiles. Adjust at your own risk.}

\subsection{\texttt{Cut Off Object Bottom (mm)}}
\index{Cut Off Object}
This setting is used to help print models that were not specifically designed for FFF printing. In particular, it is for models that do not have a flat surface to adhere to the plate. It will sink your object Xmm into the build plate, creating a nice flat surface to begin your print. You can also use this option to remove the lower portion of your model, or if carefully measured, cut your part in half for printing object as two halves.
\begin{figure}[H]
\centering
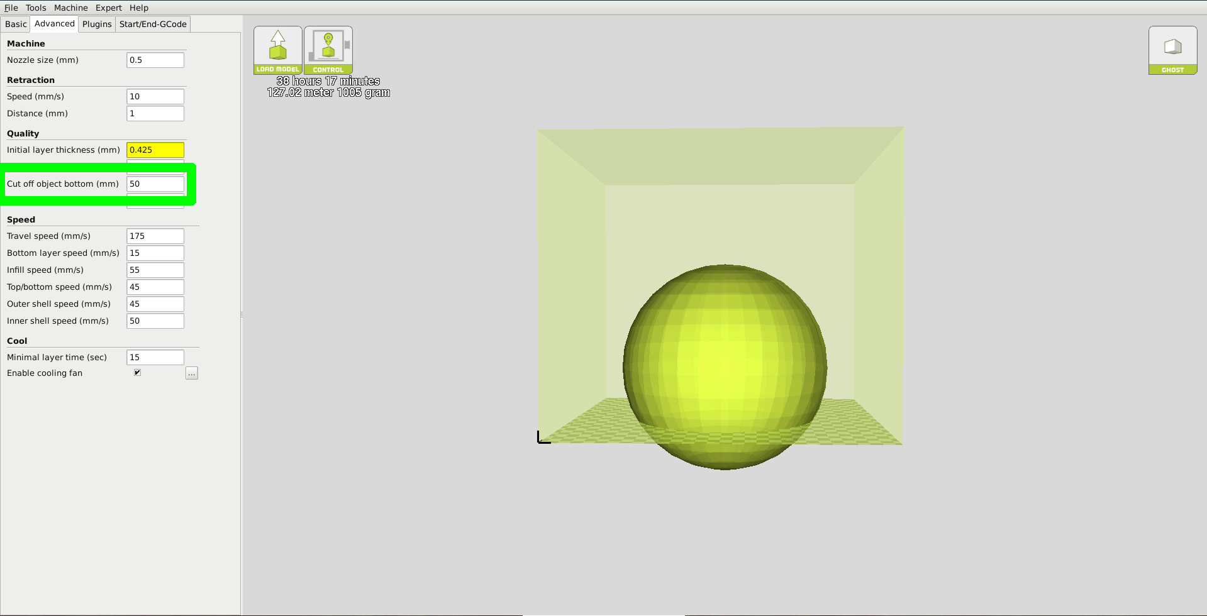
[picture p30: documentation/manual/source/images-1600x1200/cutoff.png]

\caption{Cutoff Example}
\label{fig:Cutoff Example}
\end{figure}

\subsection{\texttt{Dual Extrusion Overlap}}
\index{Dual Extrusion Overlap}
This will determine how far your Dual Extruders will overlap when laying down material. This will help adhesion between the two different colors or types of filament. This setting is only used when the printer is equipped with two hot ends and extruders.

\subsection{\texttt{Travel Speed}}
\index{Travel Speed}
This setting will determine how fast your print head moves while not extruding filament. A normal travel speed of 125 - 175mm/s is recommended.

\subsection{\texttt{Bottom Layer Speed}}
\index{Bottom Layer Speed}
This will control your initial layer speed. In general, a slower initial layer speed will help with first layer adhesion. 

\subsection{\texttt{Infill Speed}}
\index{Infill Speed}
This is how fast your print head speed will be while laying down the interior portion of your model. Faster speeds are usually tolerable here, as none of the infill will be visible from the outside of your object. If you go too fast compared to your inner and outer shells, you can have adhesion issues or blobs of filament left behind from the print head.

\subsection{\texttt{Outer Shell Speed}}
\index{Outer Shell Speed}
This will be the outermost surface of the model. This is the most important speed setting, as it controls the speed of your print head on the visible layers. As a general rule of thumb, the slower you go the better looking print you will get. 

\subsection{\texttt{Inner Shell Speed}}
\index{Inner Shell Speed}
This affects vertical walls that are in between the outer shell and infill. This will not be visible but will help support the outer shell and the infill. We recommend keeping this speed setting between your infill and your outer shell speed.

\subsection{\texttt{Minimal Layer Time}}
\index{Minimal Layer Time}
This will determine a minimum amount of time your printer will spend laying down each layer. If your layer print time falls below this your printer will automatically slow down to reach this time before moving onto the next layer. Tweaking this can help get cleaner, crisper prints.

\subsection{\texttt{Enable Cooling Fan}}
\index{Enabling Cooling Fan}
Enables operation of your extruder active cooling fan. The fan settings can be adjusted in the \texttt{Expert Settings} options.

\section{\texttt{Plugins}}
\index{Plugins}
Plugins are custom settings which will alter your print at specific points. The two that come preloaded with Cura are \texttt{Tweak at Z}, and \texttt{Pause at Height}. More plugins and information can be found here: \texttt{http://wiki.ultimaker.com/Category:CuraPlugin} To activate one of these highlight the desired plugin and click the drop-down arrow directly below the Plugins box. \textcolor{red}{These plugins affect how GCODE is generated. Use at your own risk.} \texttt{Be sure to turn these off before switching back to quick print mode. They will affect quickprint settings if left on.}
\begin{figure}[H]
\centering
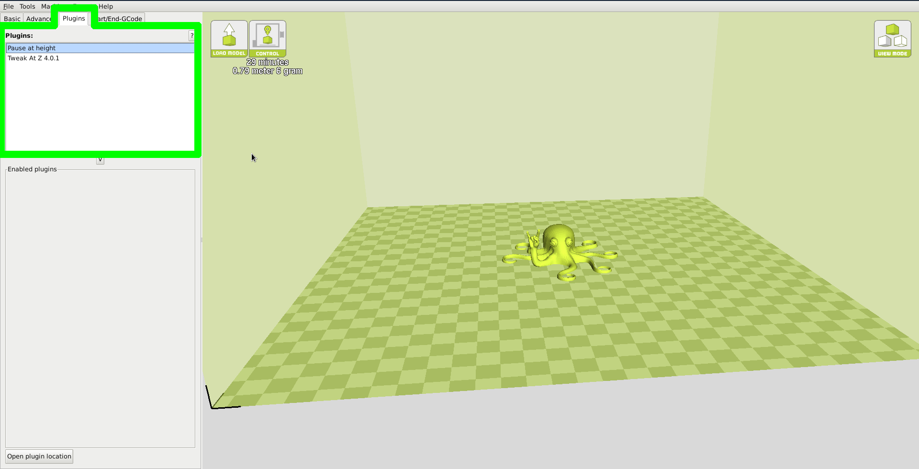
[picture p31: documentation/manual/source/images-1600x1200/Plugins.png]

\caption{View of Plugins}
\label{fig:Plugins}
\end{figure}

\subsection{\texttt{Tweak at Z}}
\index{Tweak at Z}
Make basic changes at specified Z heights. You can define the Z height or layer count at which you want to make a change. Then choose how you would like to change your settings. You can alter temperatures, fan speeds, and print speeds. Fine tuning these for specific STL files, can produce cleaner prints.

\subsection{\texttt{Pause at Z Height}}
\index{Pause at Z Height}
Pause your print at a specified height. You can also specify where to move the print head and how much filament to retract. This will prevent “blobs” from accumulating on your print while paused. This setting is most commonly used when switching colors of filaments in the middle of a print.

\section{\texttt{Start and End GCODE Settings}}
\index{Custom GCODE}
\index{Start GCODE}
\index{End GCODE}
Custom GCODE allows for complex automatic printer movements and operations. By adding custom GCODE into the start or end of your file, you can alter how it prints. A comprehensive list of GCODE commands can be found here: \texttt{http://reprap.org/wiki/G-code} We recommend new users to leave this as provided in the profiles at \texttt{https://www.lulzbot.com/cura}

%mini
\subsection{\texttt{TAZ 6 Specific Considerations}}
Please be cautious when changing any of these start and end GCODE settings. \textcolor{red}{This is where your automatic bed leveling commands are stored. If improperly altered, your printer will no longer automatically compensate for the heated bed position and can potentially damage components on the printer.} If you are uncertain of the change you are trying to make to start/end GCODE, please contact us at \texttt{Support@LulzBot.com} before hand.

\definecolor{green2}{rgb}{0.00,0.375,0.0}

\subsection{\texttt{Changing Wiping and Probing Temperatures}} \label{sssec:num1}
\index{Wiping Temperature}
\index{Probing Temperature}
We have set wiping and probing temperatures that we have found work well with specific types of filament and filament manufacturers. If you are using a type and/or manufacturer of filament not listed in the quickprint settings, you may need to adjust these temperatures for optimal probing. In the start GCODE section, there will be three separate temperatures you can adjust. What these GCODE lines do will be described in the \textcolor{green2}{green text} to the right of the command. The ones you will want to adjust are:
\begin{itemize}
\item \texttt{M109 SXXX}                    \textcolor{green2}{; soften filament for z homing}
\item \texttt{M104 SYYY}                    \textcolor{green2}{; wipe temp}
\item \texttt{M109 SZZZ}                    \textcolor{green2}{; heat to probe temp}
\end{itemize}

By changing the variables \texttt{(XXX, YYY, ZZZ),} you can change what temperature your printer will soften, wipe, and probe. Our temperatures for softening, wiping, and probing will be a good starting point for other manufacturer's filament. When making adjustments, we recommend \texttt{+/- 5°C} changes at a time. \texttt{Be sure to watch the probing sequence when experimenting with new temperatures.} Be prepared to power off the 3D printer if the probing sequence fails.

\section{\texttt{Expert Settings}}
\index{Expert Settings}
Expert settings will give you more specific options for your retraction, skirt, active cooling, infill, support, brim, raft, and special settings. To gain access to this section you go to \texttt{Expert} > \texttt{Open Full Settings} or on your keyboard press \texttt{Control + E}.
\begin{figure}[H]
\centering
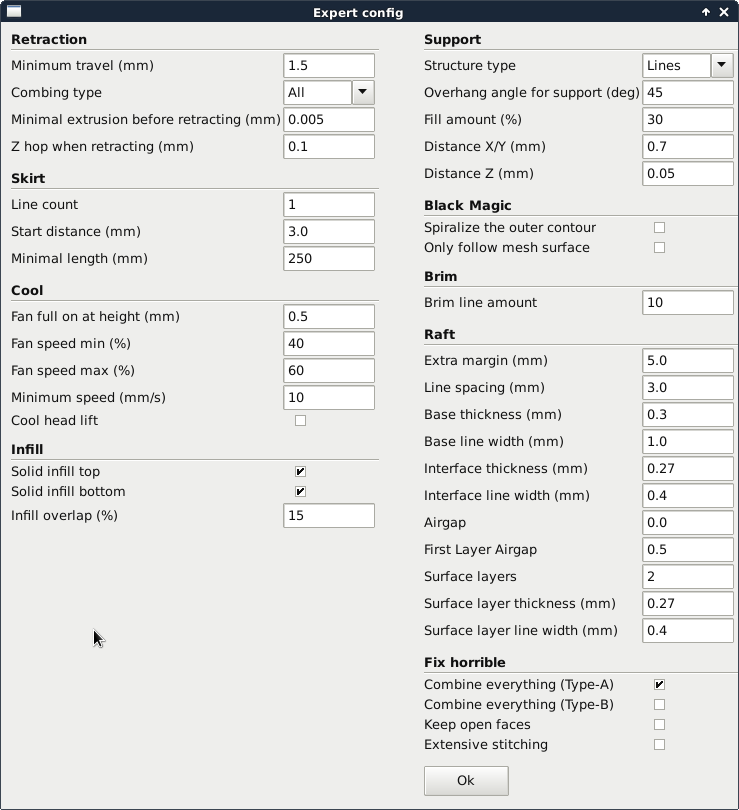
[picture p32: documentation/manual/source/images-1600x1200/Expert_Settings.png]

\caption{View Expert Settings}
\label{fig:Expert Settings}
\end{figure}

\section{\texttt{Retraction}}
\index{Retraction}
Retraction pulls filament out of your nozzle when it is not extruding to prevent your print head from dripping on your object. This section is where you will control how your extruder retracts its filament.

\subsection{\texttt{Minimum Travel}}
\index{Minimum Travel}
This sets the minimum travel distance of your print head in order to retract. If your print head is not moving this far during travel moves, it will not retract.

\subsection{\texttt{Combing}}
\index{Combing}
This option prevents your print head from traveling over holes in the X/Y plane when printing. This will slightly increase print time, but will prevent strings from getting caught on the holes during travel moves. We recommend keeping this setting on.

\subsection{\texttt{Minimal Extrusion Before Retracting}}
This will prevent a retraction move, if your extruder has not put out Xmm of filament since its last retraction.

\subsection{\texttt{Z Hop When Retracting}}
\index{Z hop}
This will raise your print head Xmm while retracting. This setting helps prevent ooze and strings from being deposited on your print. 
%\textcolor{red}{We do not recommend this setting for TAZ 3 users and earlier. This can cause issues with Z dimensional accuracy.}

\section{\texttt{Skirt}}
\index{Skirt}
Skirt creates a line around the outside of your object. Most commonly used to prime the extruder, in order to prevent missed filament at the beginning of a print. Leave this setting on. Turning this setting off will allow for utilizing the full build volume.

\subsection{\texttt{Line Count}}
\index{Line Count}
This will define the number of loops the Skirt creates around the outside of your object. Smaller models will require more loops to properly prime the extruder.

\subsection{\texttt{Start Distance}}
\index{Start Distance}
This will define the distance away from your model that the skirt will be created. 

\subsection{\texttt{Minimal Length}}
\index{Minimal Length}
This will define the minimum extruded line length for the skirt. This will over ride your line count, producing as many lines as required to reach the minimal length.

\section{\texttt{Cool}}
\index{Cooling}
This section will define how your extruder cooling fan will operate during the print. If your print speeds are slowed down due to minimal layer time, the fan will run between minimum and maximum speed based upon how much the layer is slowed down.

\subsection{\texttt{Fan on at Full Height}}
\index{Fan Settings}
This is your Z height where your fan will be turned on to its minimum percentage setting. Especially helpful with high temperature retaining filaments such as PLA. This will be scaled between 0\%, and your minimum fan speed based upon layer height; with it being disabled for the first layer.

\subsection{\texttt{Fan Speed Min}}
\index{Fan Settings}

This will be the speed your fan runs when enabled at full height. Once the Z height is reached for Fan on at Full Height, this will be the speed your fan runs at.

\subsection{\texttt{Fan Speed Max}}
\index{Fan Settings}
This is the fastest speed at which your fan will ever run. When your print speed is slowed down due to minimal layer time, your fan will run between minimum and maximum speed. The maximum fan speed is reached when your printer must be slowed by 50\% or greater.

\section{\texttt{Support}}
\index{Support Material}
You define how your support material is generated here. You must have some form of support turned on in the basic settings in order for these settings to have an effect.

\subsection{\texttt{Structure Type}}
\index{Support Settings}
You can choose between a Grid or a Line pattern for your support material. The grid will be a checkerboard pattern in the X and Y direction. The line option will produce lines in along the Y-axis for support. The grid will provide stronger support than the line option, but will be harder to remove.

\subsection{\texttt{Overhang Angle for Support}}
\index{Overhang Angle}
This will determine where support material is generated. In general you will be able to print a model with 45 to 90 degree angles in relation to the bed without support. We recommend leaving this setting at 45 degrees.

\subsection{\texttt{Fill Amount}}
\index{Fill Amount}
This will determine how dense your support material is printed, similar to Infill Percentage. The higher percentage, the better support, but it will be harder to remove the support material, will use more material, and will lead to a larger total printing time.

\subsection{\texttt{Distance X/Y}}
\index{Support}
This will determine how far away from your object in the X/Y plane that the support material is being placed.

\subsection{\texttt{Distance Z}}
\index{Support}
This will determine how far away your support material is from your object in the vertical direction. A smaller number here makes for better support, but makes it harder to remove.

\section{\texttt{Black Magic}}
\index{Black Magic}
This section allows you to transform your model into a hollow shell, a single layer thick.

\subsection{\texttt{Spiralize the Outer Contour}}
\index{Spiralize}
This causes your Z-axis to be constantly moving upward as printing your single outer wall shell. The results are no layer change lines, giving a much smoother surface. This setting is typically only used for artistic objects as they will be fragile.

\subsection{\texttt{Only Follow Mesh Surface}}
\index{Black Magic}
This will cause your print to follow the outside of your model, building it completely hollow with a single wall outer shell. The only difference between this and Spiralize, is that the Z-axis moves regularly. That is, it prints a layer and then moves up vertically to the next one.

\section{\texttt{Brim}}
\index{Brim}
Brim circles the base of the print while making contact, helping adhere the print to the heated plate. This is only one layer thick, and easily removed post-print. This section defines how the brim is formed when brim is activated in basic settings.

\subsection{\texttt{Brim Line Amount}}
This will determine the distance the brim will cover around the outside of your object. The more brim used, the better your part will adhere to the plate. 

\section{\texttt{Raft}}
\index{Raft}
Raft is a platform built underneath your object, designed to help adhesion and prevent warping. It will lay down support material, and then a platform on top of the supports. Your model will be built on top of this platform. The bottom surface of your printed part will not be as clean or as even when using this option. Raft is typically not required.

\subsection{\texttt{Extra Margin}}
\index{Extra Margin}
This determines the distance around the outside of your object that the raft is created. Can be helpful for ensuring no warping of the lower layers.

\subsection{\texttt{Line Spacing}}
\index{Line Spacing}
This will determine the spacing between “support” lines for the raft. A small spacing makes the support structures closer together improving strength of the raft, but uses more material.

\subsection{\texttt{Base Thickness}}
\index{Base Thickness}
This defines how thick your raft will be.

\subsection{\texttt{Base Line Width}}
\index{Base Line Width}
This will define how wide your “support” material is for the raft. This setting will determine how well the surface layers of the raft print.

\subsection{\texttt{Interface Thickness}}
\index{Interface Thickness}
This will determine how thick the surface layers of the raft are. The surface layers are the platform that is built upon the supports.

\subsection{\texttt{Interface Line Width}}
\index{Interface Line Width}
This will determine how wide the top layers of the platform will be. In general, you can keep this set to your nozzle size, as surface quality of the removable raft is not important.

\subsection{\texttt{Airgap}}
\index{Airgap}
This will define the distance between your raft and your print. A larger gap will make your part easier to remove, but will make the bottom of your print look worse.

\subsection{\texttt{Surface Layers}}
\index{Surface Layers}
This will determine the number of layers that create the “platform” of your raft. If you have a wide line spacing, you may want to increase this number to ensure a solid platform. 

\section{\texttt{Fix Horrible}}
\index{Fix Horrible}
These are some of the more advanced and experimental options. They are designed to help repair models with errors to make them suitable for 3D printing. \texttt{They do not always work.} Please be cautious when using these options as they can have unintended effects on your print quality.

\subsection{\texttt{Combine Everything (Type-A)}}
\index{Combine Type-A}
This will attempt to fix all external mesh errors, while keeping internal holes intact. This can accidentally fill in intentional internal holes.

\subsection{\texttt{Combine Everything (Type-B)}}
\index{Combine Type-B}
This will ignore all internal holes of the model and only focus on the external holes. This is helpful when only the outside finish of the model is important.

\subsection{\texttt{Keep Open Faces}}
\index{Open Faces}
This will ignore all manifold errors in the object. It can create issues generating the GCODE as Cura does not know how to interpret the open holes. This option should only be used if you are sure that the holes in the mesh are intended. In general, you should not use this option.

\subsection{\texttt{Extensive Stitching}}
\index{Extensive Stitching}
This causes Cura to automatically add triangle meshes in an attempt to fix manifold errors. This algorithm will greatly increase GCODE generation time and may end up adding in un-intended meshes. It is recommended that you repair your model through MeshLab, FreeCAD or your preferred CAD program before attempting this option.

\section{\texttt{Dual Extrusion}}
\index{Dual Extrusion}
The LulzBot TAZ has the ability to add dual extrusion functionality with the Dual Extruder Tool Head. We only recommend the Dual Extruder Tool Head for advanced users. Installation and operation of the dual extruder will require you to flash your firmware, calibrate your extruders, level two heads to a single plane, define extruder offsets, and fine tune your slicing profile. This can be a little overwhelming for new users. We recommended that you have a couple of months of single extruder printing experience before making the switch. 

\subsection{\texttt{Tool Head Installation Instructions}}
\textcolor{red}{Refer to appropriate Dual Extruder Tool Head Quick Start Guide for the specific steps required to install and operate your new tool head. Failure to follow the proper steps may result in damage to the tool head or 3D printer.} Installation and operating instructions are available at \texttt{OHAI.LulzBot.com/accessories}. The following steps are only meant to be an overview of the typical process.

\subsection{\texttt{Updating Firmware}}
\index{Updating Firmware}
In order to use the Dual Extruder you will need to update your firmware to activate the second hot end.

\begin{itemize}
\item Power on your 3D printer and connect it to your computer through USB.
\item Select \texttt{Machine > Machine Settings}.
\item In the top right-hand corner you will see a \texttt{Change Tool Head} button, select this. 
\item Next you will need to select the proper hot end type. Please compare photos with your existing tool head. Choose the correct hot end and select \texttt{Next}.
\item Select the photo that corresponds with your tool head and press \texttt{Next}.
%\item Select the appropriate tool head for your TAZ and select \texttt{Next}.
%\item Choose the correct nozzle size for your machine. If you are not sure what size your printer has use your serial number to determine the nozzle size with the information found at \texttt{https://www.lulzbot.com/printer-identification}.
\item The final step will be \texttt{flashing the firmware}. Choose \texttt{Flash the firmware} to be sure to update the printers firmware to the proper settings. \textcolor{red}{This must be done to allow your printer to operate properly.}
\item Once the progress bar has completed select \texttt{OK > Next > Finish}.  
\item You can verify a proper firmware update by looking at the LCD screen. You should now see three separate temperature readings. 
\end{itemize} 
You can revert the firmware back to the stock configuration for your LulzBot 3D printer by selecting \texttt{Machine > Machine Settings > Change Tool Head}. Doing so will overwrite any of your current firmware settings.
%\subsection{Preparing Cura}
%In order to slice for a second tool head, you will need to let Cura know that you have added a second tool head. 
%\begin{itemize} 
%\item Select \texttt{Machine > Machine Settings > Extruder Count > 2}.
%\item Select \texttt{Ok} to close out the screen.
%\item Select \texttt{Machine > Machine Settings} to open the Machine settings again. 
%\item A new section labeled \texttt{Extruder 2} is now present. Within it you will see an \texttt{X offset and Y offset}.
%\item Set the \texttt{X offset to 0} and the \texttt{Y offset to -50}.
%\item Select \texttt{Ok} to save your changes. The Machine settings window will close.
%\end{itemize} 
\subsection{\texttt{Calibrating Extruders}}
\index{Calibrating Extruders}
Each individual extruder will have its own unique set of Extruder steps per unit, or Esteps. Your Dual Extruder was calibrated before leaving the production floor. The number for each extruder will be located on the back of the tool head. This will need to be updated within your printer's firmware.
\begin{itemize}
%\item Load the outer and inner calibrations squares into Cura \texttt{https://www.lulzbot.com/downloads}
%\item Open the Printer Interface window and set temperatures for both heads. Switch between hot ends by entering ``\texttt{T0}'' for the rear extruder into the command line terminal. Press \texttt{enter}.
%\item Type ``\texttt{T1}'' for the front extruder into the command line terminal. Press \texttt{enter}.
%\item Make two marks at 100mm and 120mm on the filament from the top surface of each extruder.
%\item Once at the correct extrusion temperature type into the command line ``\texttt{G92}'' and press \texttt{enter}. Then ``\texttt{G1 E100 F60}'' and press \texttt{enter}.
%\item Switch to the other tool head by entering ``\texttt{T0}'' for the rear or ``\texttt{T1}'' for the front. 
%\item Type into the command line ``\texttt{G92}'' and press \texttt{enter}.
%\item Type ``\texttt{G1 E100 F60}'' and press \texttt{enter}.
%\item Measure the distance that the tool head over or under extruded. You will need to adjust your Esteps by 8 up or down for each mm it under or over extruded.
\item Update your Esteps for the rear extruder and E1steps for the front extruder through your LCD screen. \texttt{Configuration > Advanced Settings > E/E1 Steps > New Number}. Push in on the knob to exit out of the Esteps entry.
\item Store your new Esteps \texttt{Configuration > Store Memory}.
\end{itemize}

\subsection{\texttt{Defining Second Extruder Offset}}
\index{Second Extruder Offset}
To get crisper looking prints, you will want to really dial in your offsets. With the outer and inner square on your build platform, \texttt{left-click} on the outer square, then \texttt{right-click} on the inner square and select \texttt{Dual Extrusion Merge}. The red square will be printed with your front extruder, and the yellow square will be printed with the rear extruder.
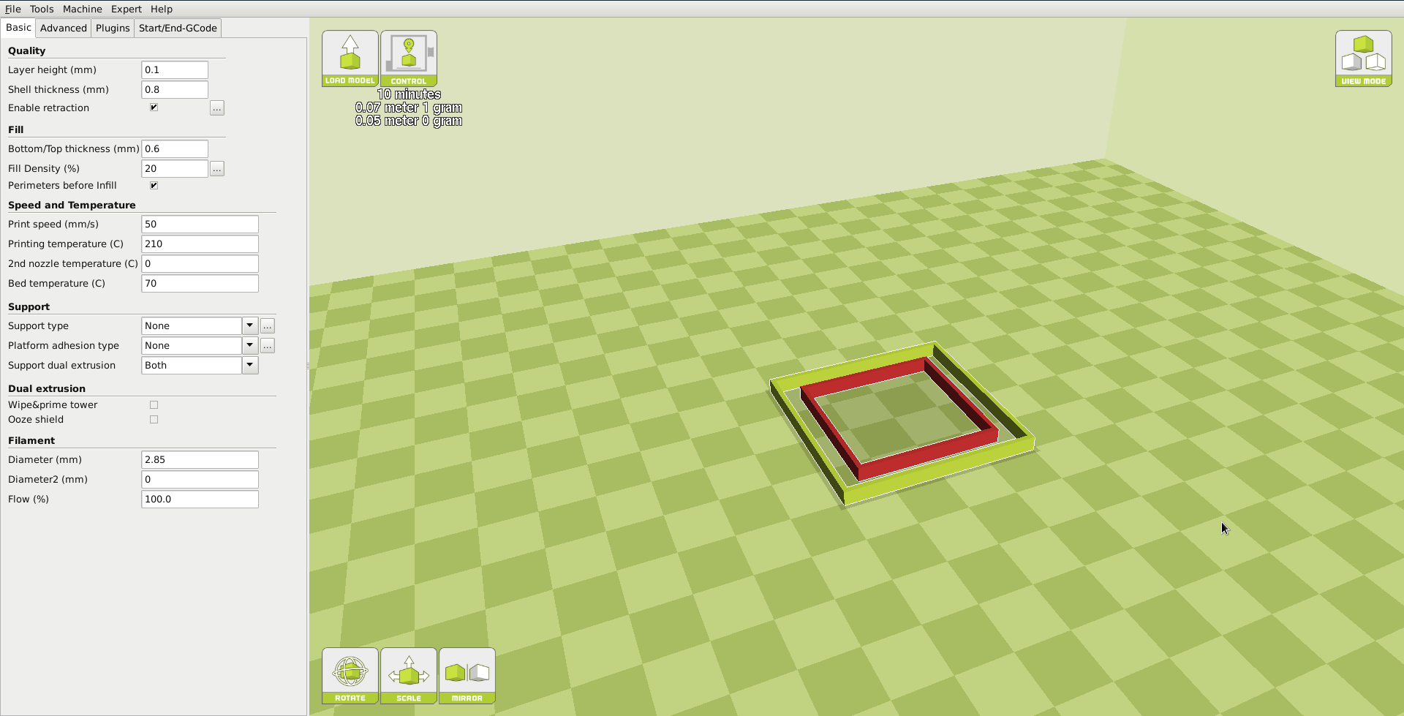
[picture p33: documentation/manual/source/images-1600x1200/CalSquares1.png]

After printing the squares, you will want to measure Top, Bottom, Left, and Right gap. Enter these numbers into our offset calculator found here: \texttt{https://www.lulzbot.com/dual-extruder-calibration-calculator} This will produce new offsets, that will need to be updated in the Machine Settings menu. Repeat as many times as desired to truly fine tune the offset. 

\subsection{\texttt{First Dual Print}}
\index{First Dual Print}
When you are ready to produce your first dual extrusion print, you will need to combine the two separate STL files. One STL file will be for each print head. \texttt{Left Click} on whichever STL you would like printed with the \texttt{Rear Tool head}. Then \texttt{Right Click} on whichever STL file you would like printed with the \texttt{Front Tool head} and select dual extrusion merge. You will now see a single model in two colors on the build plate. The red section will be printed with the front extruder, while the green section will be printed with the rear extruder. 

\begin{figure}[H]
\centering
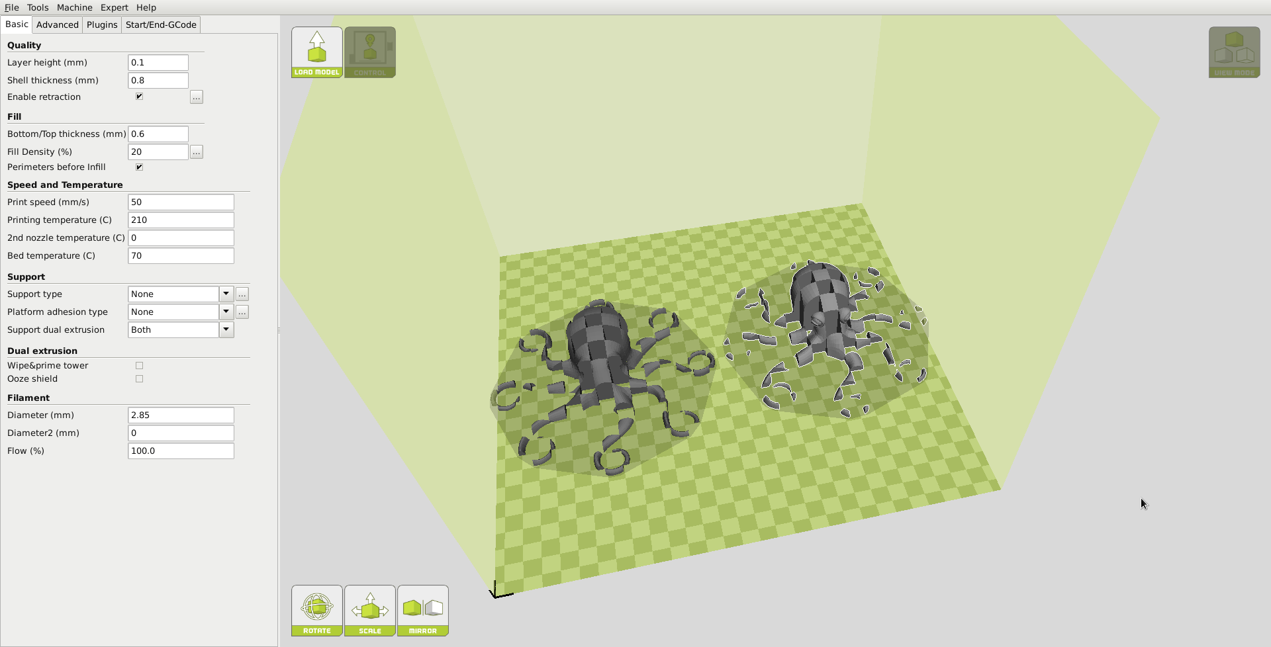
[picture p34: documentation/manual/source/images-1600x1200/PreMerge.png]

\caption{Before Merge}
\label{fig:Before Merge}
\end{figure}

\begin{figure}[H]
\centering
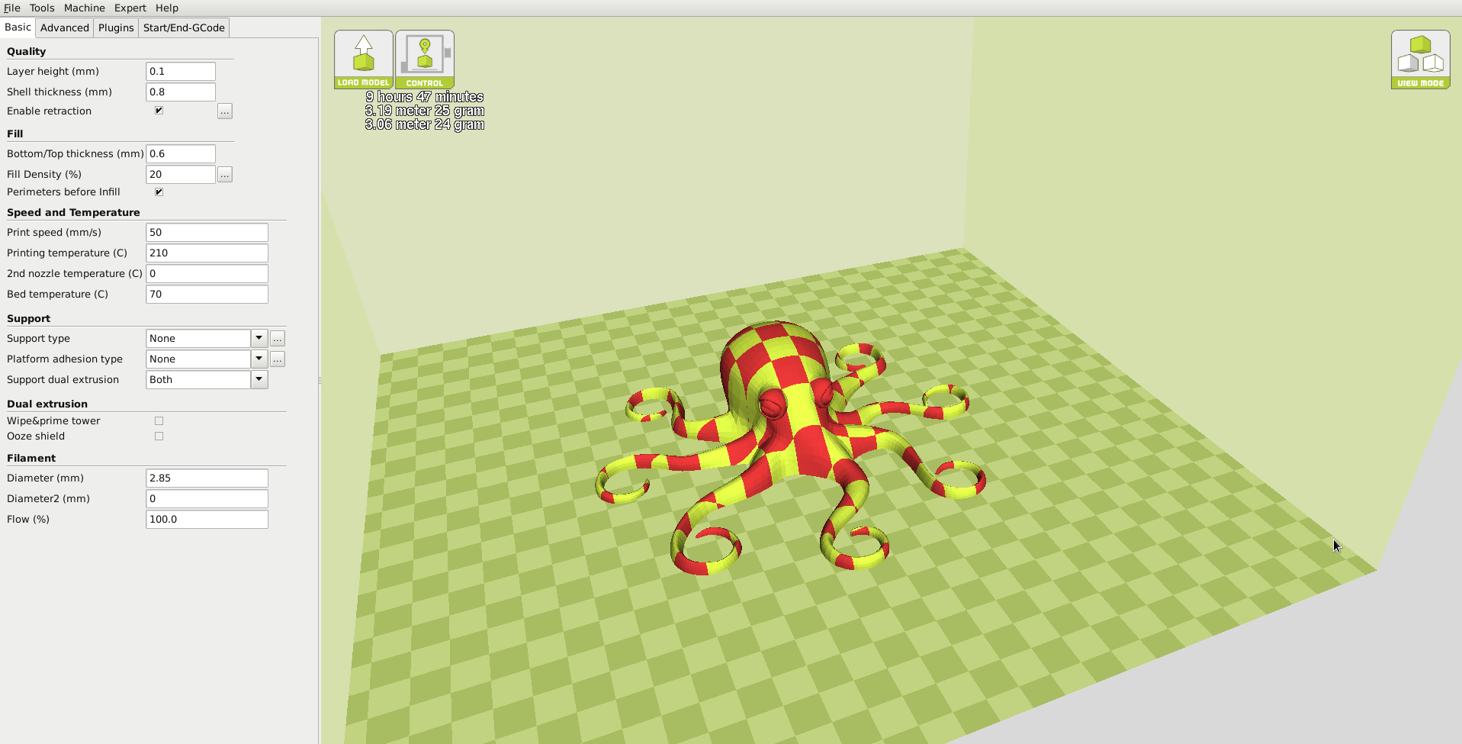
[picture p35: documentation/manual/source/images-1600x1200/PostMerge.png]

\caption{After Merge}
\label{fig:After Merge}
\end{figure}

\subsection{\texttt{First Print}}
\index{First Dual Print}
After your object has been merged as intended, you will be ready to start the print. After selecting print from your SD card or the control panel, your printer will start the probing and cleaning process. It will clean both nozzles, but only probe with the rear. If you are getting contact with your printer nozzles on previous printed parts, you will need to level the front hot end to the rear.

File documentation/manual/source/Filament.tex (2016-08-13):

%
% Filament.tex
%
% LulzBot TAZ™ User Manual
%
% Copyright (C) 2015 Aleph Objects, Inc.
%
% This document is licensed under the Creative Commons Attribution 4.0
% International Public License (CC BY-SA 4.0) by Aleph Objects, Inc.
%

%%% Copy to Setup.tex, break at the point software is needed. %%%
\index{spool holder}
\index{filament arm}
\index{filament spool}
\index{spool}
\glossary{Spool}{Plastic filament coiled and stored on a plastic reel. Preferred over 1.75-mm filament due to improved feeding and better mounting options.}
\glossary{Filament}{Plastic material in a ``string'' like form, as it is fed to the printer.}
\glossary{ABS}{Acrylonitrile butadiene styrene thermoplastic. Usually extrudes at 230C.}
\glossary{PLA}{Polylactic acid is a corn-based biodegradable polymer. Usually extrudes at 185C.}
\glossary{HDPE}{High-density polyethylene.}
\glossary{Polycarbonate}{A strong and impact-resistant thermoplastic. Usually extrudes at ~300C.}
\glossary{HIPS}{High-impact polystyrene.}
\glossary{Laywoo-D3}{Wooden filament similar to PLA. Forty percent of its content consists of recycled wood. Usually prints at ~180C to 210C. Color can be changed by varying the extrusion temperature.}

Before you start printing you will need to load a reel of filament onto the filament arm. The filament arm is meant to work with 1-kg and 5-lb plastic filament reels but can be modified to work with other reel and spool types.

\begin{enumerate}

\item You will find the filament arm on the front right-hand side of the TAZ 3D printer (Figure \ref{fig:filament_arm}, page \pageref{fig:filament_arm}). Place the filament reel on the filament arm with the filament feeding counter-clockwise.

\begin{figure}[H]
\centering

\caption{Filament reel arm}
\label{fig:filament_arm}
\end{figure}

\index{feed tube}
\item Feed the end of the filament through the filament feed tube. The filament should now be threaded through the PTFE sleeve and exit near the extruder (Figure \ref{fig:filament_arm_loaded}, page \pageref{fig:filament_arm_loaded}).

\begin{figure}[H]
\centering

\caption{Filament run through the guide}
\label{fig:filament_arm_loaded}
\end{figure}

\item Your filament reel is now mounted and ready for the next steps.

\item When changing filament, slide the opposite end of the filament through one of the holes in the hub of the filament spool. This will keep the filament from unwinding from the spool.

\end{enumerate}

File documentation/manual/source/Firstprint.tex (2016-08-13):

%
% Firstprint.tex
%
% LulzBot™ TAZ User Manual
%
% Copyright (C) 2015 Aleph Objects, Inc.
%
% This document is licensed under the Creative Commons Attribution 4.0
% International Public License (CC BY-SA 4.0) by Aleph Objects, Inc.
%

\index{bed leveling}
\section{\texttt{Bed Leveling}}
Make sure you take the time to go through the following procedure to help ensure that your prints are consistent and trouble free. Make sure to first read the instructions for using the Printrun software. Connect to the printer as described in the Printrun software section. Once \texttt{Pronterface} is connected to the printer use the homing buttons to home the X and Y axis. \textcolor{red}{Do not use the \texttt{Home Z button} until after the \texttt{Z axis End stop} has been adjusted. Make sure that the red shipping clamps on the Z axis smooth rods have been removed before continuing.}

\subsection{\texttt{Rough Adjustment of the Z Axis End Stop Trigger}}
\index{end stop}
\begin{figure}[H]
\centering

\caption{Z end stop trigger}
\label{fig:Z_end_stop_trigger}
\end{figure}
Before using the \texttt{home Z} button or the \texttt{home all} button you will need to adjust the \texttt{Z axis end stop trigger}. The red end stop trigger is on the far left of the printer, mounted on the X-axis motor mount. Once connected to the TAZ 3D printer in Pronterface, Rotate the \texttt{Z axis end stop trigger} clockwise to lower the bottom of the screw closer to the Z axis end stop. Once lowered by approximately 1cm, press the \texttt{Home Z button} to home the Z axis. The hot end will approach the heated bed and should stop around a centimeter above the surface of the heated bed. While the Z axis is moving down pay attention to the Z axis movement and sound. The Z axis stepper motors should be moving in unison. If you notice a grinding sound, stop, turn the printer off and before proceeding, make sure that the Z axis looks level in relation to the body of the TAZ 3D printer. Manually rotate one of the Z axis linear threaded rods by hand if needed to visually level the Z axis.

\index{z axis}
\subsection{\texttt{Raising the Z Axis}}
Use the \texttt{+Z 10 button} to move the Z axis up in \texttt{10mm} increments. \textcolor{red}{Commands sent in Pronterface will stack, so multiple movement button presses can potentially be harmful and cannot be stopped without powering down the 3D printer.} Keep an eye on the nozzle for the hot end. Raise the Z axis until the hot end nozzle is approximately 40-50mm away from the print bed.

\subsection{\texttt{Verify Z Axis Leveling}}
With the Z axis above the bed, use the included \texttt{150mm ruler} to measure the distance from the bottom of the \texttt{X axis} smooth rod and the top surface of the \texttt{Y axis} aluminum bed plate on the left side (Fig. \ref{fig:X-Y_axes_leveling_check}, page \pageref{fig:X-Y_axes_leveling_check}).
\begin{figure}[H]
\centering
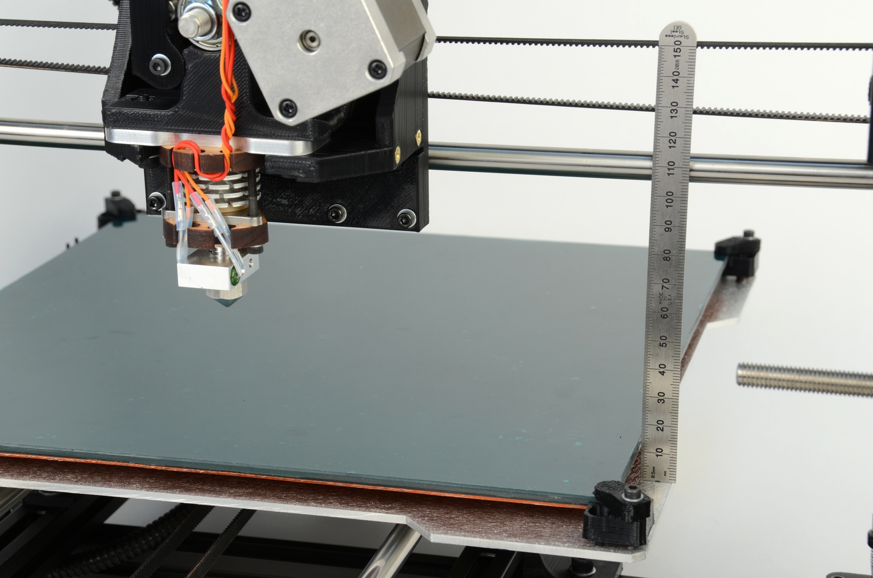
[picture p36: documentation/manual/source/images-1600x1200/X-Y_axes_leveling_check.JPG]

\caption{Verifying the X and Y axis are square}
\label{fig:X-Y_axes_leveling_check}
\end{figure}
Compare the distance measurement from the left side to the measurement on the right side. The distance measurement should be the same. If not, in Pronterface use the \texttt{Motors off} button to turn off the stepper motors on the TAZ 3D printer. Manually, by hand, turn the threaded rod on one side of the printer to raise or lower that side to match the measurement on the other side. If the Z axis has been adjusted measure again to confirm that the left and right side of the Z axis are level in relation to the Y axis aluminum plate.

\subsection{\texttt{Fine Adjustment of the Z Axis End Stop}}
\begin{comment}
\begin{figure}[H]
\centering

\caption{Z end stop trigger}
\label{fig:Z_end_stop_trigger}
\end{figure}
\end{comment}
Now that the Z axis is checked for level a finer adjustment of the Z axis end stop trigger can be set.
Adjust the \texttt{Z axis end stop trigger} by rotating the screw counter-clockwise to raise the tip of the screw. Raise the screw by roughly the same amount of the distance between the nozzle tip and the print surface. Press the \texttt{Home Z} button to home the Z axis. The tip of the nozzle should now be very close to the surface of the bed.

\subsection{\texttt{Leveling the Print Bed}}
Slide a thin piece of paper underneath the nozzle in the front left corner of the bed. Adjust the Z axis end stop and home the Z axis until the tip of the nozzle applies a firm pressure on the paper. Test by attempting to slide the paper out from under the nozzle. A gentle resistance should be felt, in addition to a visible impression on the paper. If the paper tears, the nozzle is too close. Adjust the Z axis homing height by adjusting the Z axis end stop, turning clockwise in 180 degree increments to increase the Z axis homing and turning counter-clockwise to decrease the Z axis homing height. Once adjusted, press the +Z 10 button to raise the Z axis.

Move the hot end nozzle tip over to the far side of the X axis by using the \texttt{+X 100 button}. As the X axis carriage approaches the end of the X axis use the \texttt{+X 10 button} and finally the \texttt{+X 1 button}. Once the tip of the nozzle is near the front right corner of the bed slide the same piece of paper under the nozzle and home the Z axis. Adjust the corner's bed leveling screws so that the tension felt when moving the paper under the nozzle matches the tension felt previously. To raise or lower the front right corner of the bed, adjust the screw with the spring only. Do not adjust the middle screw. Turn the screw clockwise to lower the bed, thereby decreasing the tension felt when moving the paper. Turn the screw counter-clockwise to increase the tension felt when moving the piece of paper from under the nozzle. Adjust the front right corner of the bed until the amount of tension felt when moving the piece of paper under the nozzle feels the same as the tension felt when doing the same thing on the front left corner. Once adjusted, press the +Z 10 button to raise the Z axis.

Repeat the same process using the \texttt{+Y button} to move the heated bed to place the nozzle on the rear right corner of the bed. Adjust the height of the bed using the same procedure as outlined above. Once adjusted, press the +Z 10 button to raise the Z axis. Finally, move the X axis carriage over to the rear left corner of the bed and perform the same leveling procedure to adjust the last corner.

The bed should now be almost perfectly level. We will check this in a later section. Use the controls in Pronterface to raise the Z axis up 20mm, and move the X axis carriage over to the center of the X axis.

\section{\texttt{Set Temperature}}
\index{temperature}
%Make sure to first read the instructions for using the Printrun software. Connect to the printer as described in the Printrun software section
%%% XXX pageref going to \label not \section (page \pageref{Installing Printrun}).
The TAZ 3D printer ships with a small length of ABS filament from our testing prior to shipping. The filament will need to be removed before proceeding. In order to do so set the hot end to 230C. Make sure that the \texttt{Monitor Printer} (Found in the upper middle portion of the Pronterface window) check box is selected. Once the hot end has reached 230C, gently squeeze both the idler screws and the plastic clip together and pull upwards to release the idler. Rotate the idler counter clockwise, exposing the filament and the filament drive (hobbed bolt). Remove the filament by hand by gently pulling it out. Allow more time for the filament to soften if the filament cannot be removed easily.

Set the hot end and print surface for ABS or PLA plastic and turn both on. The temperature settings for ABS should be set at \texttt{230°C} for the hot end and \texttt{85°C} for print surface; for PLA they should be set at \texttt{185°C} for the hot end and \texttt{55°C} for print surface. These temperatures work well for filament sourced from LulzBot, however you may need to adjust the temperature a degree or two depending on the filament source, color and type. Click the \texttt{Motors Off} button.
\glossary{Idler}{Refers to parts using a bearing (usually a 608ZZ) to add tension in belts or to add pressure against a rolling surface.}
\section{Load Filament}
\index{filament}
\index{hot end}

Once the hot end is heated to the correct temperature you will now need to load the plastic filament into the extruder.
\begin{figure}[hbt]
\centering
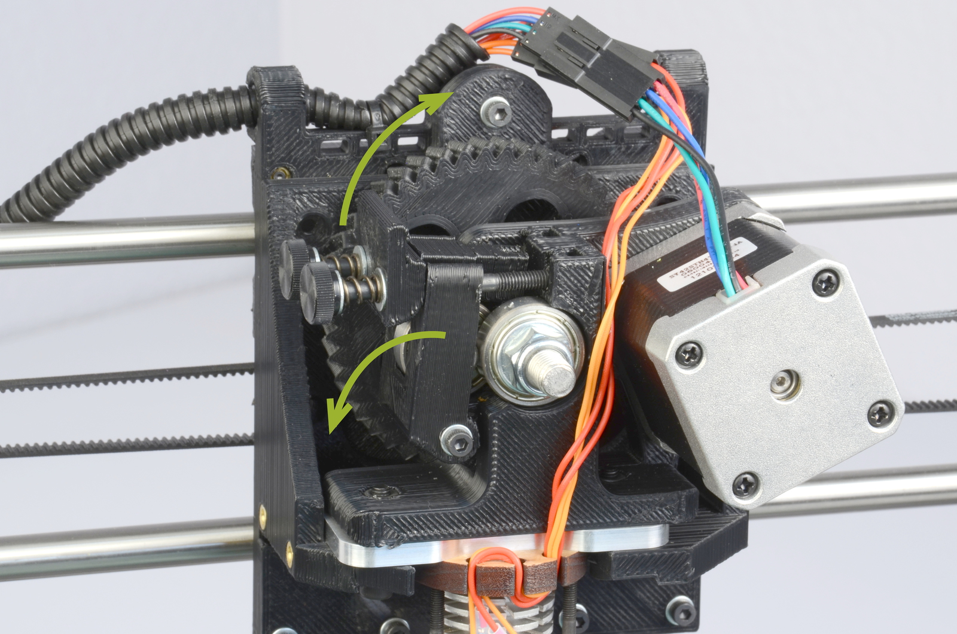
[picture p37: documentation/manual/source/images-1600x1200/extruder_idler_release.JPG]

\caption{Extruder idler release}
\label{fig:extruder_idler_release}
\end{figure}
% update feed hole picture.
Gently squeeze both the idler screws and the plastic clip together and pull upwards to release the idler (Fig. \ref{fig:extruder_idler_release}, page \pageref{fig:extruder_idler_release}). The idler screws can be loosened if necessary. The idler can be rotated downwards allowing access to the hobbed bolt and filament feed hole(Fig. \ref{fig:extruder_filament_slot}, page \pageref{fig:extruder_filament_slot}). If the extruder has a small section of filament already loaded, you will need to remove the filament once the extruder idler has been opened, by gently pulling out the filament by hand once the hot end has reached extrusion temperature. From the previously installed filament reel, feed the end of the plastic filament into the filament feed hole
(Fig. \ref{fig:extruder_filament_slot}, page \pageref{fig:extruder_filament_slot}).
\begin{figure}[hbt]
\centering
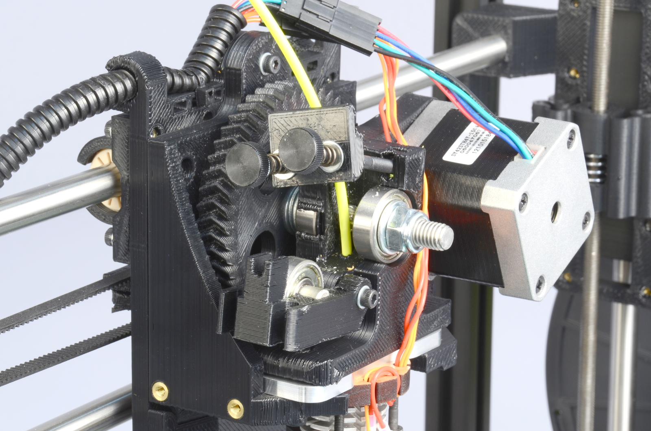
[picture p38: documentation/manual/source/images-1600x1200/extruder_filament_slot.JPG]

\caption{Extruder filament slot}
\label{fig:extruder_filament_slot}
\end{figure}
Now you can push the filament through the extruder by slowly pushing the filament down into the hot end.

Once the filament extrudes a small amount out of the nozzle by manually pushing the filament into the extruder body raise the idler and slide the two idler bolts and plate back into place. Tighten the two idler bolts if you previously loosened them. Tighten the two screws until they are finger tight, then tighten them slightly more, until the top of the thumbscrews are about 10mm away from the plastic clip. In Pronterface, in the lower left hand corner of the screen there are two text entry boxes next to the ``Extrude'' and ``Reverse'' buttons. In the top text entry box (length in mm) change the 5 to 40. In the lower box (Speed in mm/min) change the 300 to 250. Now use the \texttt{Extrude} button in Pronterface to test that the extruder is working properly. You may need to extrude 40-60mm of filament to fully prime the hot end. Slowly tighten the two extruder thumbscrews while extruding until you achieve reliable, repeatable extrusion. If the extrusion stalls you may need to open the extruder and trim off any filament with a chewed out section.

\section{\texttt{Home Printer}}
Use the home buttons to home the X axis and then the Y axis. Next home the Z axis. When the Z axis is at home the nozzle tip should be right above the glass
(Fig. \ref{fig:nozzle_height}, page \pageref{fig:nozzle_height}). The image to the left, in figure \ref{fig:nozzle_height}, is the correct nozzle height.
\begin{figure}[p]
\centering
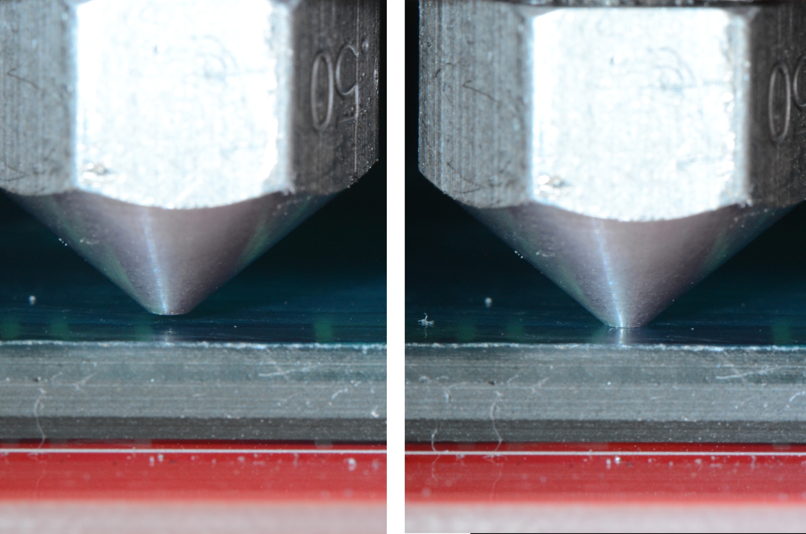
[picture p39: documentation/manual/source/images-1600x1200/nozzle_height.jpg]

\caption{Nozzle height}
\label{fig:nozzle_height}
\end{figure}
\begin{figure}[p]
\centering

\caption{Z end stop trigger}
\label{fig:Z_end_stop_trigger}
\end{figure}
The nozzle should not be pushing down on the print surface. To lower or raise the Z home height adjust the Z end stop trigger. The red end stop trigger is on the far left of the printer mounted on the X-axis motor mount.
(Fig. \ref{fig:Z_end_stop_trigger}, page \pageref{fig:Z_end_stop_trigger}).
The red end stop trigger can be lowered by turning clockwise and raised by turning counter-clockwise. Once you have homed the axes and the hot end and bed have reached the correct temperature it is time to print!

%fix image positioning, images for 5.3 get shoved underneath 5.4
\section{\texttt{Z Print Height}}
Load the \texttt{bed\_level.gcode} file.
This file can be found in the calibration directory on the SD card included with your TAZ 3D printer or at: \texttt{http://www.LulzBot.com/support/downloads}. Place your mouse cursor over the entry \texttt{Bed Level Check}, right click and select \texttt{Save as}} Once you have downloaded the file to your computer, press the \texttt{Load file} button in Pronterface. Navigate through the file browser to the downloaded \texttt{bed\_level.gcode} file, highlight the file and select the \texttt{Open} button.

The .gcode file should appear in the Pronterface G-Code viewer. Press the \texttt{Print} button to begin the print. When the print starts make sure the first layer is not printing too close or too far from the print bed. Note
Figure \ref{fig:1st_layer_adhesion}, page \pageref{fig:1st_layer_adhesion},
\begin{figure}[hbt]
\centering
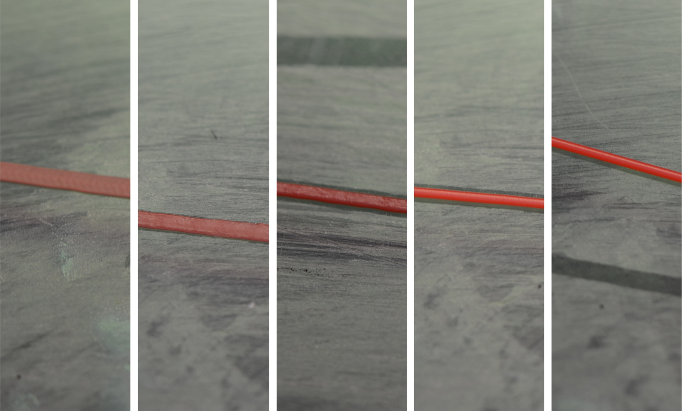
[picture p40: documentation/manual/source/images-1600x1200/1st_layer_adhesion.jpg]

\caption{First layer adhesion}
\label{fig:1st_layer_adhesion}
\end{figure}
as an example of a good first layer adhesion. From left to right: very low, low, \emph{perfect}, high, very high. If the first layer is too high or low you can pause the print by pressing the \texttt{Pause} button. Adjust the Z end stop trigger. After making adjustments remove any printed material off the bed and home the axes and press \texttt{Restart} to restart the print. Measure the extrusion width, ideally the width would be the same in all areas of the bed. You would raise/lower a corner to minimize/increase the extrusion width to match the others. Once they are all consistent, the bed is level.

\section{\texttt{Your First Octopus!}}
Load the \texttt{octopus.gcode} file. This file can be found at:
\texttt{http://download.lulzbot.com/TAZ/3.0/novelties/}. Load the file in Pronterface, bring the hot end \texttt{(230C ABS/185C PLA)} and the heated bed \texttt{(85C ABS/60C PLA)} up to printing temperature. Once the printer is at the appropriate temperature, press the \texttt{Print} button to begin the print.

\section{\texttt{Remove Part}}
After the part is finished printing, the heated bed will automatically cool down to room temperature. If you are printing PLA you will need to turn the heated bed off. Once the bed cools you can you pop the finished part off of the printed surface. To remove the printed part, use the clam knife included in your printer kit. Leather gloves are suggested to protect your hands from the clam knife blade. It is also safe practice to not place your hand in the direction you are pushing the clam knife. Using the side of the clam knife blade pry up one side of the printed part. If your part is large you may need to pry at multiple points to pop the part off of the print surface. When removing parts take caution to not damage the PET film. If the film is cut or ripped it will peel from the glass and need to be replaced. Make sure to reset the heated bed to the correct temperature and allow it to heat up to the needed temperature before starting the next print.

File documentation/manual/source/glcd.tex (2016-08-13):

%
% glcd.tex
% Graphical LCD.
%
% LulzBot® TAZ User Manual
%
% Copyright (C) 2015 Aleph Objects, Inc.
%
% This document is licensed under the Creative Commons Attribution 4.0
% International Public License (CC BY-SA 4.0) by Aleph Objects, Inc.
%

The Graphical LCD Controller, or GLCD, allows you to print with the LulzBot TAZ 3D printer without needing to have a computer connected or using host software such as Cura LulzBot Edition. This will allow for more efficient space in the workspace and free up a computer for other tasks.

In the following sections you will find general information on using the GLCD, how to transfer .gcode files to the included SD card, heat up the printer, start a print, and make configuration adjustments.

\section{\texttt{Graphical LCD Controller, Cura or Other Host?}}
\label{sec:Graphic LCD, Cura or Other Host?}
The Graphical LCD Controller is perfect for normal day to day printing and will be used in the majority of your print jobs. However, in some instances, you will want to use Cura instead of the GLCD. A few examples of when you would want to plug the USB cable back in and use Cura:
\begin{itemize}
	\item A number of manual movements are required to perform calibration checks. Because of this it is easier and faster to make the required manual movements within Cura. Calibration checks can be done with the GLCD, but require a number of repetitive menu selections. 
%%%%%	\item Printrun offers a number of extra options for advanced users, including custom gcode input, output display, and pronsole. Pronsole is the command line portion of Printrun that can be used in scripts for automation or controlling a printer through remote access, for example, SSH.
	\item Cura is the preferred printer host software, as the inclusion of quick print profiles, the combination of slicing engine, and printer host communications allows for easy all-in-one use.
\end{itemize}

\section{\texttt{Multiple Connections}}
Because the LulzBot TAZ 3D printer can be controlled by the GLCD and by host software, caution is advised when connecting to the printer through USB as the print can be interrupted when connecting or disconnecting the USB cable. A general rule is: once you have started a print with either the GLCD, Cura, or another printer host, for the rest of the print use only that controller. When printing with the GLCD, never try to connect through USB in the Cura host software; wait until the print is complete, and then connect in Cura.

\section{\texttt{Putting Print Files on the SD Card}}
To print from the GLCD, transfer .gcode print files onto the SD card. Follow the normal steps, as explained in the Cura chapter, to create .gcode print files on your computer. Insert the SD card into your computer using a SD reader slot or USB SD card reader. Open a file browser- / -manager and locate the created .gcode files; drag and drop or paste the .gcode files to the SD card. Once the files have transferred, eject the SD card from your computer and insert it back into the SD card slot on the left side of the printer, at the top near the GLCD.

\section{\texttt{Printing With the Graphical LCD Controller}}
\begin{figure}[b]
\centering
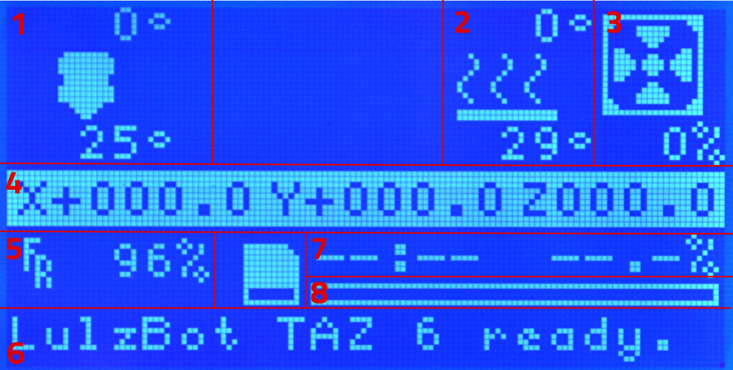
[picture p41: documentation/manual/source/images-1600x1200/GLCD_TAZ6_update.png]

\caption{GLCD Info Screen}
\label{fig:info_screen}
\end{figure}

\subsection{\texttt{The Graphical LCD Controller Status Screen}}
The GLCD screen will turn on you power up your LulzBot TAZ 3D printer. The start-up screen will display the Status screen (fig. \ref{fig:info_screen}, page \pageref{fig:info_screen}). The Status screen is the default screen for the GLCD, presenting the current status of the printer. There are a number of live statuses shown on the Status screen; these will give you current temperatures, tool head coordinates, print status, and more. The different numbered sections of the status screen are shown in Figure \ref{fig:info_screen} above. Follow the key below for more information on each section.

\begin{enumerate}
\item Hot end temperatures: represents the current temperature (bottom) and set temperature (top) of up to three nozzles. The RAMBo control electronics currently only supports two hot ends.
\item Heat bed temperature: represents the current temperature (bottom) and set temperature (top) of the heat bed.
\item Fan speed: represents the current optional extruder fan speed. The fan is set to off (0\%) by default; the fan is not recommended for ABS. If you print with PLA filament, you will want to use the fan. If cooling is turned on in Cura, this portion of the display will change to reflect the .g-code embedded extruder fan control instructions.
\item Tool head coordinates: represents the current tool head coordinates on the X, Y, and Z axes.
\item Feed rate: represents the current feed rate setting. The feed rate is set to 100\% by default; this matches the speed set in the gcode generation. When on, the status screen selection knob can be turned to increase or decrease the feed rate during the print. Increasing/decreasing the feed rate will increase/decrease the speed of the print.
\item Printer status: lists the current status of the printer including: SD card status, current printing file, or completed print time.
\item Current print time: lists the length of time for the current print job.
\item Progress bar: represents the progress of the current print job. The print is finished when the bar is completely white.
\end{enumerate}

\subsection{\texttt{Using the Selection Knob}}
To navigate through the GLCD menu use the selection knob by rotating to scroll through selections and pressing the knob to make a selection. From the main status screen, press the knob to move into the menu screen (Figure \ref{fig:main_menu}, page \pageref{fig:main_menu}). To move backwards in the menu tree, select the top most menu selection on the current screen. Selections that will move you backwards through the menu tree are noted by an upwards-facing arrow. Note that if the menu is left idle it will automatically move back to the main status screen.

\begin{figure}[h]
\centering
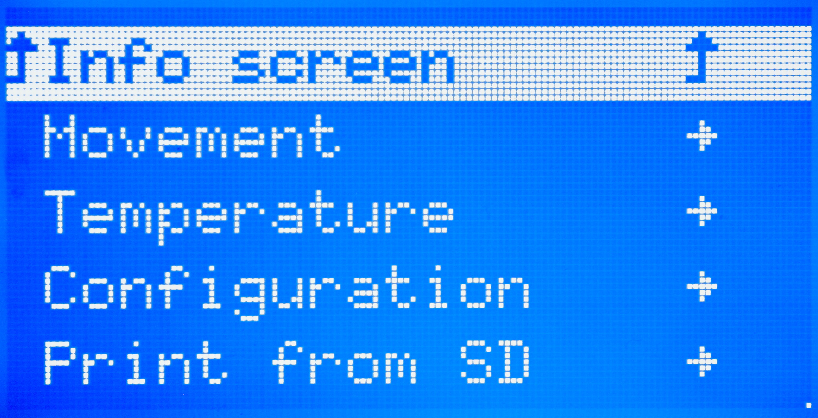
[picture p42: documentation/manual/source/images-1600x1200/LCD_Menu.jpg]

\caption{Main Menu}
\label{fig:main_menu}
\end{figure}

%\subsection{\texttt{Preparing for a Print}}
%Before starting a print you will need to set the hot end and heat bed to the appropriate temperatures for the filament type you are using. To quickly set the printer to preheat, click the selection knob to bring up the menu and select \texttt{Temperature}. Select \texttt{Filament Type} to automatically set the hot end and bed temperature for that specific filament.

%If you need to set the extrusion and/or bed temperature to a setting different than the preheat temperature you can manually set the temperature. To do so, from the main menu navigate through: Temperature \texttt{->} Custom Temp \texttt{->} Nozzle or Bed. Clicking on either of these settings will give you a menu to set and select the desired temperature setting.

\subsection{\texttt{Selecting a File From the SD and Starting a Print}}
Once the SD card has the desired GCODE file loaded onto it, you can begin your first print. From the main menu select the \texttt{Print from SD} option. You will now see a selection of the directories and .gcode files on the SD card. Navigate through the menu to locate the file you would like to print. Select the desired file to begin the print.

\subsection{\texttt{Making Manual Movements With the Graphical LCD Controller}}
As noted previously (page \pageref{sec:Graphic LCD, Cura or Other Host?}), making numerous manual movements is easier done using Cura. However, you can make manual movements with the GLCD. Navigate to \texttt{Movement -> Move Axis}. You will select the length of the movement and then which axis to move. %\texttt{Note; that only 1-mm and 0.1-mm movements are allowed for the Z-axis and extruder.}

When at the move screen; turn the selection knob clockwise to move the axis in millimeters in the positive direction and counter-clockwise for the negative direction. 

\subsection{\texttt{Tune}}
Once you begin a print, you will notice your movement option changes to tune. This section will allow you to make changes to individual settings while a print is running. You can adjust overall speed, nozzle temperature, bed temperature, flow \%, check apprx layer height, and even change filament. \texttt{When adjusting these settings, we recommend making small changes at a time.}

\subsection{\texttt{Change Filament}}
You can change filament through the GLCD mid print by going to \texttt{Tune -> Change Filament}. This will park your print head in the front left corner, and wait for you to resume the print. During this time you can change colors, or even types of filament. Once your filament change has completed, press in your GLCD knob to continue where it left off. \texttt{If you manually move the tool head while changing filament, your printer will lose place of it's position.}

\section{\texttt{Configuration Options}} 

%\begin{figure}[H]
%\centering
%\includegraphics[keepaspectratio=true,angle=0,height=0.4\textheight,width=1.0\textwidth]{LCD_Menu.jpg}
%\caption{Main Menu}
%\label{fig:main_menu}
%\end{figure}

Out of the box, the LulzBot TAZ 3D printer is already calibrated for printing. However, the GLCD does allow tuning of the more advanced configuration settings. \textcolor{red}{We highly suggest you not modify the configuration settings unless you are certain it is necessary}. The configuration section contains settings that control how your printer operates.

\subsection{\texttt{Changing EEPROM Settings}}
\index{eeprom settings}
The \texttt{Store Memory} and \texttt{Load Memory} functions will store and load the changes you make using the GLCD. You must use the \texttt{Store Memory} function to save the adjusted settings when the printer is powered on. If you ever need to revert to the original factory settings navigate to \texttt{Control} \texttt{->} \texttt{Restore Failsafe}. Clicking \texttt{Restore to Factory} will set all configuration settings back to the original factory settings in the firmware.

For more information on the configuration settings please see the LulzBot TAZ support page at \texttt{LulzBot.com/support}.

\section{\texttt{Advanced Settings}}
In the advanced settings, you can control/modify your Z offset, maximum velocity, acceleration, jerk, and esteps/mm. Once again \textcolor{red}{we highly suggest you not modify the configuration settings unless you are certain it is necessary}. Making incorrect adjustments of these settings can have adverse affects on your prints, and potentially damage your machine.

\subsection{\texttt{Z Offset}}
\index{Z Offset}
Your LulzBot TAZ 3D printer has the ability to change the first layer height (Z offset) directly through the GLCD, even while printing the first layer. Using the GLCD, navigate to \texttt{Configuration -> Advanced Settings -> Z Offset}. While in this screen you can rotate the GLCD knob counter-clockwise to bring your nozzle closer to the print surface, and rotate it clockwise to bring it farther away from the bed. \texttt{Push in the GLCD knob to save your settings.}

\begin{figure}[H]
\centering
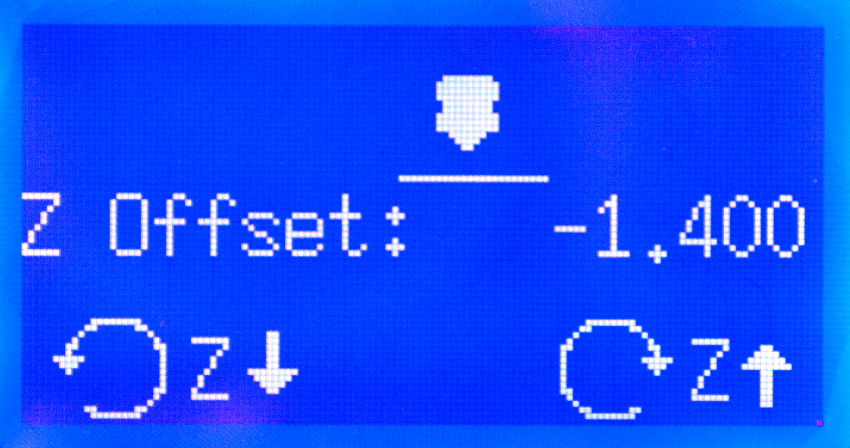
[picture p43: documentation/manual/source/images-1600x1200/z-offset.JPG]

\caption{Z Offset Screen}
\label{fig:Z_offset_screen}
\end{figure}

%\subsection{\texttt{Change Filament}}
%While printing from SD card, you can change filament by going to \texttt{Tune -> Change Filament}. This will park your print head in the front left corner, and eject the filament from the hot end. Once you have swapped filament, go to \texttt{Tune -> Resume Print}. In order to get a crisp, clean color change you will need to manually push filament through the head until the previous color has been purged. 

%To find the configuration settings, navigate to the main menu and then select \texttt{Control} (Figure \ref{fig:configuration_menu}, page \pageref{fig:configuration_menu}). In the Control configuration settings you will find temperature and motion settings. Among others, these settings include default temperature settings and axis steps per millimeter.

\subsection{\texttt{Acceleration}}
Acceleration is the derivative of speed, and determines how quickly your print head and bed will reach defined speeds. We have this set to 500mm/s\textsuperscript{\miniscule{2}} to help prevent resonance and shadowing. This can be increased for sharper corners and faster turns, however it can lead backlash issues.

\subsection{\texttt{Jerk Settings}}
Jerk is the derivative of accleration and will determine the maximum speed change allowed at any given time. \texttt{VXY- Jerk} will control jerk setting for your X and Y-axis. \texttt{VZ - Jerk} will control the jerk setting for your Z-axis. \texttt{VE - Jerk} will control the jerk settings for your extruder.

\subsection{\texttt{Vmax}}
The Vmax settings will determine the maximum speed that your printer can move on any specific motor(s). We recommend leaving these settings as is. Increasing these speeds too much can lead to skipped steps and/or binding. There will be an individual section for \texttt{X, Y, Z, and Extruder} motors. 

\subsection{\texttt{Vmin}}
This sets the minimum overall speeds. We have this set to 0 by default to allow greater control through your preferred slicing program. 

\subsection{\texttt{VTrav Min}}
This will set the minimum travel speed when the tool head is not extruding. We have this set to 0 by default to allow greater control through your preferred slicing program. 

\subsection{\texttt{Amax}}
The \texttt{Amax} settings will allow you to define a maximum acceleration limit for each motor. Increasing these may reduce print time, but can result in in shadowing and resonance issues.

\subsection{\texttt{A-Retract}} 
This sets the maximum acceleration for retraction moves of the extruder. Going too high can lead to stripping, and going too low can lead to dripping. We have this set to 3000mm/s\textsuperscript{\miniscule{2}} by default.

\subsection{\texttt{Steps/mm}}
Your LulzBot TAZ 3D printer is factory calibrated on all axis for accurate movement. These settings control that movement, and if adjusted your objects will not come out at the proper dimensions. \textcolor{red}{\texttt{We only recommend adjusting your Esteps/mm}} as this can be fine tuned for individual tool heads and filaments. 

\subsection{\texttt{Graphical LCD Controller Menu Map}}
\begin{figure}[H]
\centering
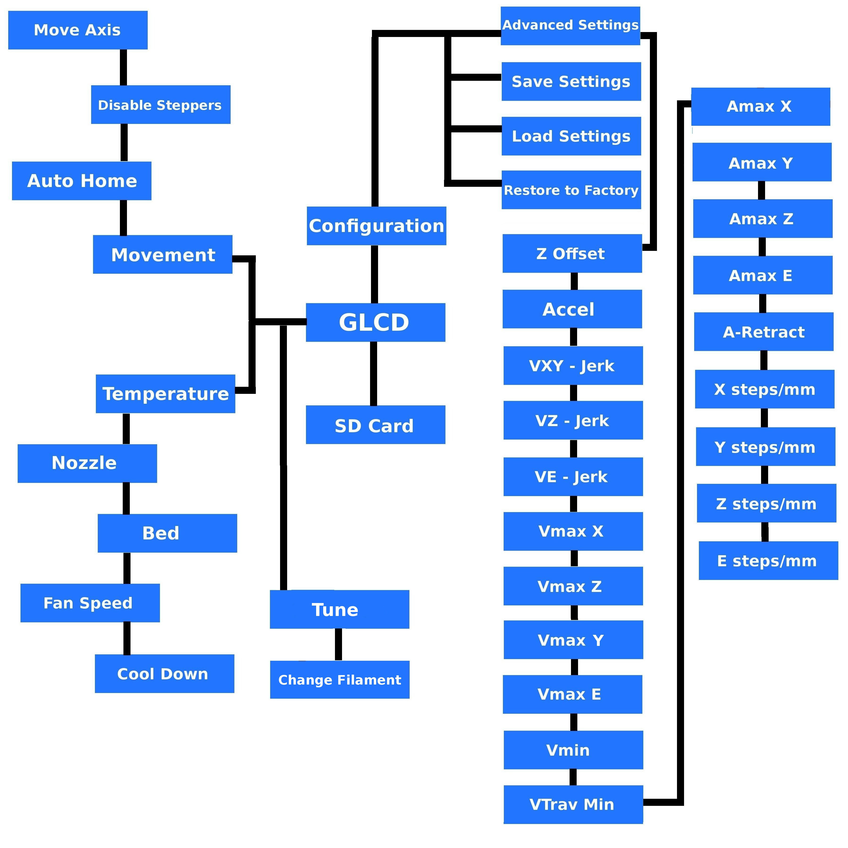
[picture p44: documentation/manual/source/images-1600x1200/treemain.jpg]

\caption{GLCD Map}
\label{fig:GLCD_Map}
\end{figure}

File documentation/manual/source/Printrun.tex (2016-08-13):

%
% Pronterface.tex
%
% LulzBot® TAZ User Manual
%
% Copyright (C) 2016 Aleph Objects, Inc.
%
% This document is licensed under the Creative Commons Attribution 4.0
% International Public License (CC BY-SA 4.0) by Aleph Objects, Inc.
%

\index{pronterface}
\index{Printrun}
\index{pronsole}
\index{plater}
\index{stl}
\index{extruder}
\index{extrusion}
\index{temperature}
\index{gcode}
\index{SD card}
\newpage
\section{\texttt{Printrun}}
\label{Printrun}
Website: \texttt{http://www.github.com/kliment/Printrun}
The host software, Printrun, can be used to start up and control your 3D printer (Figure \ref{fig:Printrun}, page \pageref{fig:Printrun}).
\begin{figure}[hbt]
\centering
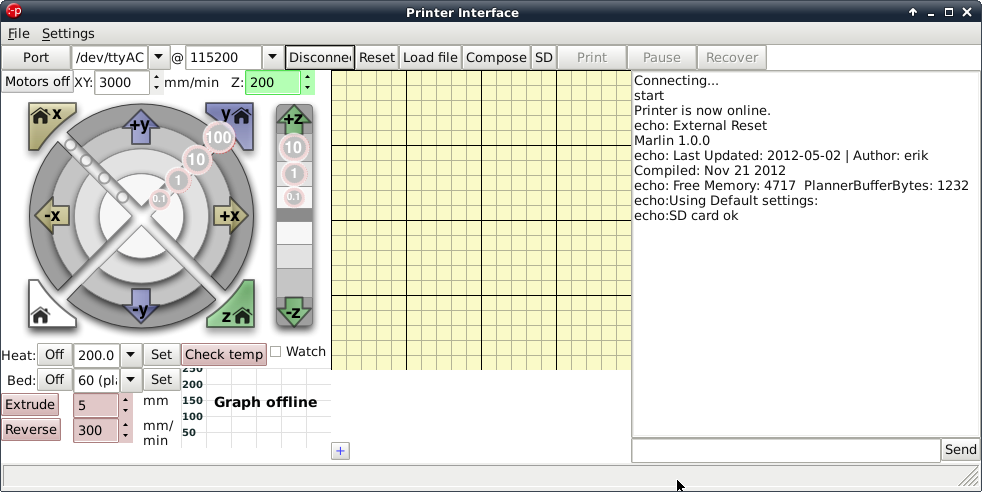
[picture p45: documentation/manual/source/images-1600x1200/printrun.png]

\caption{Printrun application for 3D printer control}
\label{fig:Printrun}
\end{figure}
The host controls include: setting the extruder and print surface temperatures, manual control of each axis, and manual extrusion. The host is also where you can push print files (\texttt{.gcode}) to the 3D printer or load print files from the SD card for printing out model designs.

\subsection{\texttt{Installing Printrun}}
Printrun contains several different applications that can be used to control the LulzBot TAZ 3D printer. It can be installed on Windows, Mac OSX and Linux based computers. Pronterface is the graphical user interface for Printrun. \texttt{Pronsole} allows printing from the command line, and can be used for scripting and some automation. \texttt{Plater} allows you to arrange and combine several STL files into one. More information on the other programs within the Printrun package can be found at \texttt{https://github.com/kliment/Printrun}. Printrun can be downloaded from \texttt{LulzBot.com/downloads}. Download the version for your operating system and extract. You will need an archive manager to extract the files. If you do not have one installed we recommend using 7-zip, which can be downloaded for free at \texttt{www.7-zip.org}.

\begin{itemize}
\subsection{\texttt{Windows Instructions}}
\index{Windows}
\item Once downloaded, extract the \texttt{dist} folder to a location of your choice. You can rename the \texttt{dist} folder if you like. Double click \texttt{pronterface.exe} to run Pronterface.

\subsection{\texttt{Mac OSX Instructions}}
\item Once downloaded, extract the \texttt{dist} folder to a location of your choice. Once extracted, double click the \texttt{pronterface-mac.app} file to install.

\subsection{\texttt{Linux Instructions}}
%\begin{itemize}
\subsubsection{\texttt{Debian|Ubuntu}}
\subsubsection{\texttt{Recommended Installation}}
\item We recommend using the stand-alone Printrun option found at \texttt{https://www.LulzBot.com/downloads}. Once downloaded and extracted, navigate to the extracted directory. Install the dependencies by issuing the following command in a terminal: \texttt{sudo apt-get install python-serial python-wxgtk2.8 python-pyglet}. Once the dependencies have been installed, run Pronterface by using the following command in a terminal: \texttt{python pronterface.py}.

\subsubsection{\texttt{Installing from source}}
\item Using Git, in a terminal issue the following command: \texttt{git clone https://github.com/kliment/printrun.git}
\item Once downloaded, change to the Printrun directory. You will need to ensure that the following dependencies are met. They are listed in the README.md file. You can use this command to install the dependencies:
\texttt{sudo apt-get install python-serial python-wxgtk2.8 python-pyglet python-tornado python-setuptools python-libxml2 python-gobject python-pip avahi-daemon libavahi-compat-libdnssd1}
followed by:
\texttt{pip install -r requirements.txt}
To install in a terminal issue the following command:
\texttt{sudo python setup.py install}.
Run Printrun by issuing the following command:
\texttt{python pronterface.py}

\subsubsection{\texttt{Fedora}}
\item Use this command to install Printrun from the official sources: \texttt{sudo yum install printrun}

\subsubsection{\texttt{Archlinux}}
\item Use this command to install Printun from AUR: \texttt{yaourt rintrun}

\end{itemize}

\index{Printrun}
\section{\texttt{Using Printrun}}

%\begin{figure}[hbt]
\begin{figure}[H]
\centering

\caption{Printrun}
\label{fig:Printrun}
\end{figure}

Printrun is used to control the printer from a computer. It is divided into 4 main parts: The buttons over the top are used to connect to the printer, load files and start \& stop prints.

The movement controls are on the left hand side, with the G-code preview window in the center and the Log window and Terminal command entry box on the right hand side (Figure \ref{fig:Printrun}, page \pageref{fig:Printrun}).

\subsection{\texttt{Connecting to the your 3D Printer}}
\index{connecting}
\index{Printrun}
\index{USB cable}
\index{port}
\index{baud rate}
\glossary{Baud Rate}{Refers to the speed at which the host controller communicates with the 3d Printer electronics.}
To start up the printer, first you will need to connect to the printer with Printrun. Make sure you have connected the USB cable from your PC to the printer before launching Printrun. If not, close Printrun, connect the USB cable, and relaunch Printrun. To connect to the printer, select the correct port by using the drop down arrow and selecting the active port, generally \texttt{/dev/ttyACM0}). On other operating systems the port may be named such as \texttt{COM1} or \texttt{tty.usbserial-USB-ID}. The \texttt{Port} button will refresh the Port listing. Once selected choose the default \texttt{115200} buad rate and press \texttt{Connect}. Pronterface will open a connection to the printer and display firmware information in the Log window.

In the text output window you will see multiple return lines. If you see \texttt{Printer is now online} you have successfully connected to the printer. The printer control buttons on the left will also darken and become click-able after connecting. If nothing is displayed in the Log window verify you have the correct port and connection speed selected. When you need to disconnect the printer simply press the \texttt{Disconnect} button.

%\begin{figure}[hbt]
\begin{figure}[H]
\centering
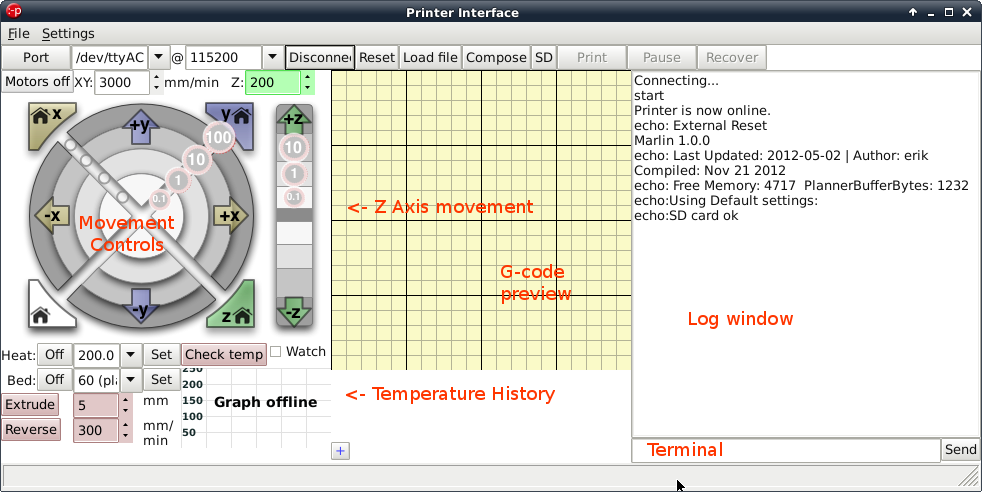
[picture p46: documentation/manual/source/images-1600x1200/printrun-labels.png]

\caption{Printrun Functions}
\label{fig:Printrun-labels}
\end{figure}

\subsection{\texttt{Movement}}
%\begin{figure}[hbt]
\begin{figure}[H]
\centering
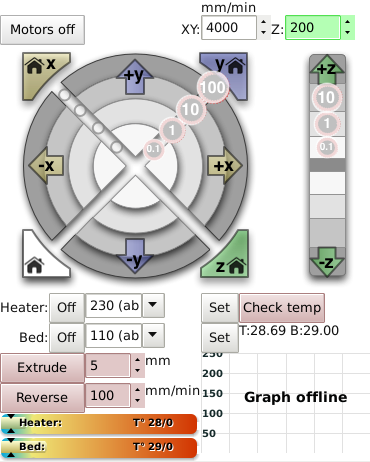
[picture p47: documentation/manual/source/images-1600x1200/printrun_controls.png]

\caption{Movement Controls}
\label{fig:Printrun_controls}
\end{figure}

\subsubsection{\texttt{Motors off}}
Your 3D printer can be moved on all three axes independently. If you would like to do so by hand, use the \texttt{Motors off} button to unlock all the stepper motors. Once unlocked they can be moved by hand. Keep in mind that there is no positional feedback, so if you move an axis you will need to re-home in order to re-establish the hot end's position.

\subsubsection{\texttt{mm/min XY:/ Z:}}
These settings control the manual jog speeds when driven with Pronterface. Use caution when changing these figures. Moving the axes too fast can cause the printer to miss steps. If that occurs with the Z axis, it can potentially cause the Z axis to become out of square.

\subsubsection{\texttt{Homing}}
\index{end stops}
Caution: when homing, the axis will continue to move in the negative direction until the end stop switch is activated. If the printer is ever transported make sure the end stop switches are clear before resuming printing. If an axis has missed an end stop and is continuing to try to move in the negative direction, immediately turn the power switch to the off position.

Each axes can be homed either individually or together. Press the \texttt{Home X} button to move the X axis to the left until it activates the end stop. Once the X axis end stop is activated, the X axis carriage will `bounce'. It will move over and move back to the home position more slowly. Press the \texttt{Home Y} button to home the Y axis. The Y axis platform will move away from you towards the rear of the printer. %The Z home button functions the same, but the Z trigger cannot be adjusted manually on the printer and uses the automatic bed-compensating routine at the beginning of each print.

\subsubsection{\texttt{X/Y/Z Axes Movement Controls}}
Prior to moving the X, Y, or Z axis, make sure that you home each axis. The X, Y and Z axes can be moved utilizing the circular movement controls. Each axis can be moved in either fine moves or large moves, ranging from 0.1mm to 100mm.  For example, to move the \texttt{Y Axis} towards you, move your mouse to the \texttt{+y} section until both the \texttt{+y} and the \texttt{100} are highlighted then select that ring section. To move the \texttt{Y axis} away from you, move your mouse to the \texttt{-y} section until both the \texttt{-y} and the \texttt{100} are highlighted then select that ring section. The X axis can be moved in a similar fashion.

The Z axis movement control operates similarly, but the movement scale is different. The Z axis will move in 0.1mm, 1mm and 10mm increments. The top half of the movement bar will move the Z axis up, by the selected units, while the lower half will move the Z axis down, by the selected units.

\begin{comment}
\section{Slic3r}
\index{gcode}
\index{STL}
\glossary{STL}{stereolithography file, also known as standard tessellation language; STL file is the common 3D model file format.}
\index{CAD}
\index{resolution}
\index{Slic3r}
Website:  \texttt{http://www.slic3r.org}

The Slic3r software is the first tool in the chain of 3D printing software
(Figure \ref{fig:slic3r}, page \pageref{fig:slic3r}).
\begin{figure}[hbt]
\centering

\caption{Slic3r application, STL to .gcode generator}
\label{fig:slic3r}
\end{figure}

Slic3r uses commonly used \texttt{.STL} files to create \texttt{.gcode} files. Gcode files contain instructions for the 3D printer on where, when, and how quickly to make movements. However, .gcode programming is not very suitable for CAD and 3D design. This is where Slic3r and the \texttt{.STL} file comes into use. The \texttt{.STL} file is a 3D model file that can be exported by all common CAD and 3D modeling software. The Slic3r software then slices the \texttt{.STL} 3D model into layers and print paths to create a 3D-printable \texttt{.gcode} file.

To launch Slic3r navigate to the \texttt{Slic3r} directory and launch the \texttt{slic3r.pl} file. On GNU/Linux operating systems you may need to set the \texttt{slic3r.pl} file as executable. It may be called \texttt{slic3r.exe} on other operating systems.

\index{download}
Slic3r includes very simple settings that allow you to easily refine prints. You can create multiple configurations for changing printer setups including nozzle sizes and desired print resolution. For ease of use we have pre-defined Slic3r configurations. They are available in the Support/Downloads section at \texttt{www.LulzBot.com}. Download the configurations to your \texttt{Slic3r} directory.

\index{configuration}
\subsection{Loading Configurations}
To load configurations, press the \texttt{Load Config...} button. In the file browser that opens, locate the downloaded configuration files. Select the configuration file that matches the nozzle size currently installed on the printer (0.5-mm nozzle is installed by default). Press \texttt{Open} and the pre-defined configuration will load into Slic3r. You can also save custom configurations for yourself by pressing the \texttt{Export Config...} button. A file browser will open that allows you to define a name and save your custom configuration.

\index{STL}
\index{plater}
\subsection{Loading .STL files}
To load an \texttt{.STL} 3D model file into Slic3r, activate the Plater tab and click the \texttt{Add...} button. In the file browser navigate to the \texttt{.STL} you wish to load and click \texttt{Open}. The silhouette of the model will appear in the Plater diagram. To print more than one copy of the model at a time, select the model name from the list and click the \texttt{More} button. With each press of the \texttt{More} button, an additional copy of the model will be added to Plater. To remove a copy of the model, select the model name again and click \texttt{Less}. To completely remove the model from Plater, select the model name and click \texttt{Delete}.

\index{gcode}
\subsection{Export .gcode files}
Once you have finished setting your part(s) in Plater you can generate the .gcode by clicking \texttt{Export G-Code...}. In the file browser, navigate to where you would like to save the \texttt{.gcode} file and list a name to save the file as. Click \texttt{Save} and Slic3r will begin generating the \texttt{.gcode} file. When Slicer is finished you will receive a prompt. If you have created a plate with multiple model designs, you can also use the \texttt{Export STL...} function to save an \texttt{.STL} file to quickly reproduce the same plate of models.

\section{Printrun}
%%% XXX shouldn't have to do it this way.
%%% HOWTO get page number from section? Ala  sec:Printrun
\label{Printrun}
\index{extruder}
\index{extrusion}
\index{temperature}
\index{gcode}
\index{SD card}
\index{Printrun}
Website: \texttt{http://www.github.com/kliment/Printrun}

The host software, Printrun, can be used to start up and control your 3D printer
(Figure \ref{fig:Printrun}, page \pageref{fig:Printrun}).
\begin{figure}[hbt]
\centering

\caption{Printrun application for 3D printer control}
\label{fig:Printrun}
\end{figure}
The host controls include: setting the extruder and print surface temperatures, manual control of each axis, and manual extrusion. The host is also where you will push print files (\texttt{.gcode}) to the 3D printer or load print files from the SD card for printing model designs.

\index{pronterface}
\index{GNU/Linux}
To launch Printrun, navigate to the \texttt{Printrun} directory and launch the \texttt{pronterface.py} file. On GNU/Linux operating systems you may need to set the \texttt{pronterface.py} file as executable. Depending on your environment you may need to launch the program by using the full command: \texttt{python pronterface.py}. On other operating systems the file may be called \texttt{pronterface.exe}.

\subsection{Connecting the Printer}
\index{connecting}
\index{Printrun}
\index{USB cable}
\index{port}
\index{baud rate}
\glossary{Baud Rate}{Refers to the speed at which the host controller communicates with the 3d Printer electronics.}
To start up the printer, first you will need to connect to the printer with Printrun. Before launching Printrun, make sure you have connected the USB cable from your PC to the printer. If not, close Printrun, connect the USB cable, and relaunch Printrun. In the top left \texttt{Port}, pull-down menu select the correct port for the printer (generally \texttt{/dev/ttyACM0}). On other operating systems the port may be named \texttt{COM1} or \texttt{tty.usbserial-USB-ID}. If you have only one printer connected, there will only be one port available to select. Make sure the port baud rate is set to \texttt{115200} in the pull-down menu to the right of the port selection. You can refresh the USB ports, by clicking the \texttt{Port} button.

Now, to connect to the printer, click the \texttt{Connect} button. In the text output window you will see multiple return lines. If you see \texttt{Printer is now online} you have successfully connected to the printer. The printer control buttons on the left will also darken and become click-able after connecting. When you need to disconnect the printer simply press the \texttt{Disconnect} button.

\subsection{Printer Controls}
\index{Printrun}
\index{hot end}
All of the printer controls can be found on the left side of the Printrun interface
(Figure  \ref{fig:Printrun_controls}, page \pageref{fig:Printrun_controls}).
\begin{figure}[hbt]
\centering

\caption{Printrun controls}
\label{fig:Printrun_controls}
\end{figure}
To set the hot end and print surface temperature, first click the \texttt{Monitor Printer} check box on. This will enable the printer temperature bars and graph. The hot end and print surface controls are labeled \texttt{Heater} and \texttt{Bed}. Select the temperature setting by using the pull-down menu for pre-defined temperature settings. You can also set custom temperature settings by typing into the temperature box.

\index{temperature}
To turn on the hot end and/or printer surface, click the respective \texttt{Set} button. The \texttt{Set} button will highlight orange when the temperature is set to ``On'' for that component. When the hot end or print surface is set to ``On'' you will see the temperature bar and graph display the set temperature and the current temperature. When both components have reached the correct temperature, the printer is ready for printing. Clicking the \texttt{Off} button will turn off that component and highlight the \texttt{Off} button blue.

\index{extrude}
\index{hot end}
Below the temperature controls are the manual extrusion controls. There you can manually extrude plastic through the hot end and retract the plastic filament from the hot end. The \texttt{Extrude} button will feed the amount of plastic, set to the right in millimeters, into the hot end. The rate at which the plastic is fed is set below the extrusion length (mm/min). The \texttt{Reverse} button will perform the opposite of \texttt{Extrude}, pulling the plastic filament back out of the hot end.

\index{manual controls}
\index{axes}
\index{X axis}
\index{Y axis}
\index{Z axis}
The large pattern of buttons above the temperature controls are the axes manual controls. These functions allow you to manually move each of the three axes of the printer. The circular pattern of four quadrants controls the X and Y axes. The top and bottom quadrants move the Y axis; the top in the positive direction (forward) and the bottom in the negative direction (backward). The left and right quadrants move the X axis; the left in the negative direction (left) and the right in the positive direction (right).

Each quadrant is split into four sections that control the length of movement by 0.1mm, 1mm, 10mm, or 100mm. The innermost section moves the axis 0.1-mm, with each section outwards becoming a larger movement, with the outside section moving the axis 100-mm.

The linear control bar to the right controls the Z axis. The Z axis is also separated into multiple movement lengths: 0.1mm, 1mm, and 10mm. The upper three buttons move the Z axis up and away from the printer surface; the three lower buttons move the Z axis closer to the print surface.

\index{home}
The four triangular buttons around the circular pattern are the axes home buttons. Each home button will move that axis in the negative direction until the end stop is activated. There is a home button for the X, Y, and Z axes. There is also a white ``Home ALL'' button that homes all of the axes at once.
\end{comment}

\begin{comment}
\subsection{Loading print files}
\index{load files}
\index{gcode}
\index{Printrun}

To load a \texttt{.gcode} file into Printrun click the \texttt{Load file} button. Navigate to the \texttt{.gcode} file in the file browser and click \texttt{Open}. You will now see a 2D image of the first layer of your model design in the .gcode viewer
(Figure \ref{fig:Printrun_viewer}, page \pageref{fig:Printrun_viewer}).
\begin{figure}[hbt]
\centering
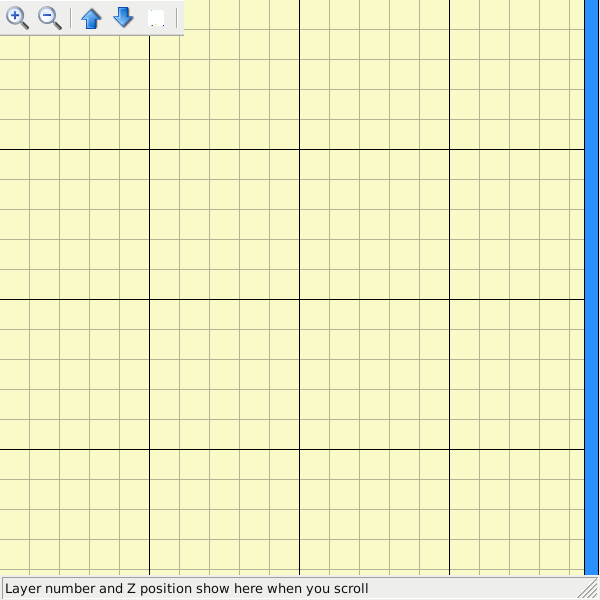
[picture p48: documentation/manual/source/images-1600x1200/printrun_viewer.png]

\caption{Printrun viewer}
\label{fig:Printrun_viewer}
\end{figure}
Click the .gcode viewer window to see a more detailed version of the sliced model. In the pop-up .gcode viewer you can zoom in using the mouse scroll wheel and flip through layers with the up and down arrow keys. To pan within the window, left-click and drag to move around the work plane. The lines shown in the .gcode viewer represent the path the extrusion nozzle will follow to print the model.

For more information on using Printrun, see the Printrun page in the Support/Downloads section at \texttt{https://www.lulzbot.com/?q=support}. Instructions for running a print can be found in the Starting the First Print section in this manual.
\end{comment}

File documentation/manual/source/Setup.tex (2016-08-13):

%
% Setup.tex
%
% LulzBot™ TAZ User Manual
%
% Copyright (C) 2015 Aleph Objects, Inc.
%
% This document is licensed under the Creative Commons Attribution 4.0
% International Public License (CC BY-SA 4.0) by Aleph Objects, Inc.
%

\section{\texttt{Hardware Setup}}
\begin{enumerate}
\item Your printer has been calibrated and tested, however, after unpacking all of the components you will need to re-mount the Y axis onto the frame and connect the bed and Y axis connectors. You will also need to re-mount the extruder tool head. Please follow the steps completely to make certain that the extruder tool head and Y axis are re-mounted correctly. You will then be on your way to your first print. Use Fig. \ref{fig:axes} to see which direction the three axes move, as the following instructions will reference the X, Y, and Z axes.

\begin{figure}[H]
\centering

\caption{Axes movement directions}
\label{fig:axes}
\end{figure}

\item Place the TAZ frame and Y axis assembly on a flat and level surface. Move to the Y axis assembly and find the four Y axis bolts. The four bolts located on the Y axis aluminum frame bars, have large plastic knobs that allow the bolts to be easily turned by hand (Fig. \ref{fig:Y_axis_bolts}, page \pageref{fig:Y_axis_bolts}). Turning counter clock-wise, remove each of the four Y axis bolts and set aside (Fig. \ref{fig:remove_Y_axis_bolts}, page \pageref{fig:remove_Y_axis_bolts}).

\begin{figure}[H]
\centering

\caption{Locate the four Y axis bolts}
\label{fig:Y_axis_bolts}
\end{figure}

%\begin{figure}[hp] CD changed to force pic placement
\begin{figure}[H]
\centering
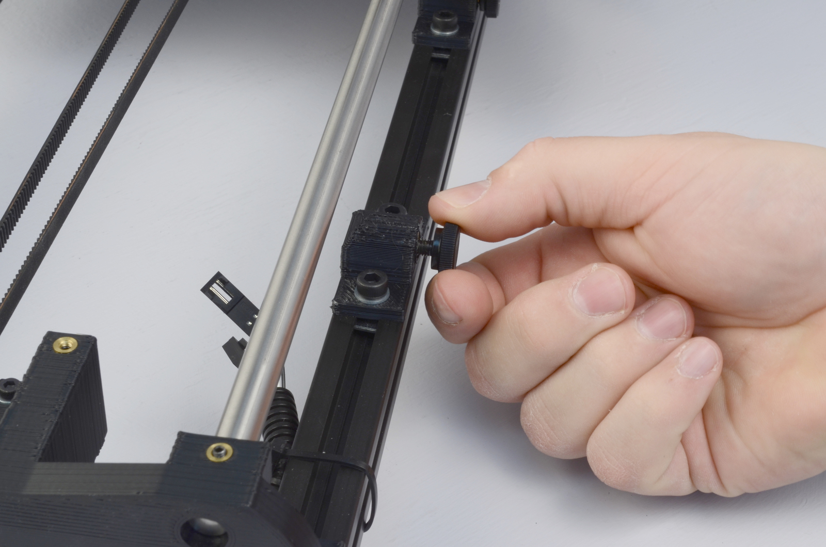
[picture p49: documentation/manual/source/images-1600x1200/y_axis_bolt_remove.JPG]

\caption{Remove the four Y axis bolts}
\label{fig:remove_Y_axis_bolts}
\end{figure}

\item On the TAZ frame locate the four Y axis mount brackets shown in Fig. \ref{fig:frame_Y_axis_mounts} (pg. \pageref{fig:frame_Y_axis_mounts}). With the print surface facing up and the stepper motor end of the Y axis facing back, slide the Y axis assembly in between the Y axis mount brackets. The four Y axis mount brackets will line up with the Y axis bolt holes on the Y axis assembly. Thread the four Y axis bolts through the brackets, into the Y axis assembly (Fig. \ref{fig:Y_axis_bolts_tighten}, page \pageref{fig:Y_axis_bolts_tighten}). Before completely tightening the Y axis bolts make sure the Y axis aluminum bars are pushed down against the TAZ frame lower bars. While pushing on the black Y axis square extrusions tighten the four Y axis bolts. The printer can now be set flat on the table.
%\begin{figure}[hp] CD forcing image placement
\begin{figure}[H]
\centering

\caption{Locate the four Y axis mounts on the frame}
\label{fig:frame_Y_axis_mounts}
\end{figure}

%\begin{figure}[hp] CD forcing image placement
\begin{figure}[H]
\centering

\caption{Screw in and tighten the four Y axis bolts}
\label{fig:Y_axis_bolts_tighten}
\end{figure}

\item The next step of installing the Y axis is connecting the print surface connectors and Y axis connectors. Pull the print bed completely to the front of the printer to get access to the Y axis connectors. You will find matching male and female 4 pin stepper motor connectors and two pin end stop connectors. Connect the matching male and female connectors (Fig. \ref{fig:Y_axis_connectors}, page \pageref{fig:Y_axis_connectors}); make sure the connector's lock clicks to be sure that it is secured.

\begin{figure}[H]
\centering

\caption{Connect the two connectors found at the rear of the Y axis}
\label{fig:Y_axis_connectors}
\end{figure}

\item Locate one of the three small black zip ties that are included in the documents bag. Wrap and tighten the zip tie around the Y axis wiring and the black Y axis frame extrusion as shown in figure \ref{fig:Y_axis_connectors_zip-ties} (page \pageref{fig:Y_axis_connectors_zip-ties}).

\begin{figure}[H]
\centering

\caption{Wrap and tighten a zip tie around the Y axis wires to the Y axis frame.}
\label{fig:Y_axis_connectors_zip-ties}
\end{figure}

\item Locate the two connectors to the left of the print bed. Connect the matching female and male large two pin heat bed connectors and the small two pin thermistor connectors, again making sure the connectors lock(Fig. \ref{fig:bed_connectors}, page \pageref{fig:bed_connectors}).

\begin{figure}[H]
\centering

\caption{Connect the two connectors on the left of the print bed}
\label{fig:bed_connectors}
\end{figure}

\item Locate the other two small black zip ties that are included in the documents bag (Fig. \ref{fig:bed_connectors_strain_relief}, page \pageref{fig:bed_connectors_strain_relief}). Wrap the two zip ties through the slot, located on the left rear of the aluminum bed plate, and around the print bed wires (Fig. \ref{fig:bed_connectors_strain_relief_done}, page \pageref{fig:bed_connectors_strain_relief_done}). Tighten the zip ties snug so the wire cannot move freely. Cut off the excess end of the zip ties with the needle nose pliers included in the tool bag.

%\begin{figure}[hp] CD forcing image placement
\begin{figure}[H]
\centering

\caption{Locate the two zip ties found in the bag with the manual}
\label{fig:bed_connectors_strain_relief}
\end{figure}

%\begin{figure}[hp] CD forcing image placement
\begin{figure}[H]
\centering

\caption{Tightly wrap the zip ties around the bed wires and through the strain relief slot}
\label{fig:bed_connectors_strain_relief_done}
\end{figure}

\item \textcolor{red}{Before proceeding make sure that the four red shipping clamps on the Z axis smooth rods have been removed.}

\item Move the X axis carriage to the center of the smooth rods. If you have not already done so, remove the foam from between the X axis carriage and the left hand X axis end. Locate and remove, with the included 2.5mm hex driver, the tool head M3 screw in top center of the X axis carriage (Fig. \ref{fig:tool_head_screw}, page \pageref{fig:tool_head_screw}). Place the extruder tool head mount onto the X axis carriage bottom first. The extruder mount will slide into the bottom portion of the carriage and self center (Fig. \ref{fig:tool_head_placement}, page \pageref{fig:tool_head_placement}).Make sure that the tool head mount is fully seated. Use the 2.5mm driver and the previously removed M3 screw to secure the extruder tool head onto the X axis carriage.
\begin{figure}[hp]
\centering

\caption{Remove the tool head screw}
\label{fig:tool_head_screw}
\end{figure}

\begin{figure}[hp]
\centering

\caption{Mount the extruder tool head}
\label{fig:tool_head_placement}
\end{figure}

\begin{figure}[hp]
\centering

\caption{Connect the two tool head connectors}
\label{fig:tool_head_connectors}
\end{figure}

\item Connect the stepper motor and the hot end to the existing wiring harness located at the top of the X axis carriage. Connect the extruder assemblies' 4-pin connectors: match the orange/red wire connector pair for the hot end and the mixed color wired connector pair for the extruder motor (Fig. \ref{fig:tool_head_connectors}, page \pageref{fig:tool_head_connectors}). Connect the matching pairs together so they lock and click.

\item Now that the Y axis is mounted and the extruder tool head is installed you should set your printer on a stable, flat, and level surface large enough for extra space around the printer. Make sure your printer work space is clear of anything that could obstruct the movement of the printer. Move the Y axis to the back of the printer to ensure unobstructed movement of that axis. \textcolor{red}{Make sure there are no flammable fabrics or liquids near the printer space}. It is also best to not put your printer near a drafty window or air conditioner vent.

\index{power supply}
\index{USB cable}
\item Unwrap the power supply and USB cables.

\textcolor{red}{MAKE SURE THE POWER SUPPLY IS COMPLETELY UNPLUGGED BEFORE MOVING ON TO THE NEXT STEP}.

\index{electronics receptacles}
\item Locate the power supply and USB receptacles along the back of the TAZ electronics enclosure
(Fig. \ref{fig:electronics_plugs}, page \pageref{fig:electronics_plugs}). Locate the power supply and the included AC power cable (Fig. \ref{fig:power_supply}, page \pageref{fig:power_supply}). Locate the DC power cable plug on the power supply. Connect the DC locking plug into the DC connector on the TAZ electronics enclosure (Fig. \ref{fig:ps_plug}, page \pageref{fig:ps_plug}). The plug is keyed which may require rotating the plug until the keys line up and the plug can be pushed in. Once you have pushed in the plug turn the locking sleeve clockwise until it is tight against the electronics enclosure (Fig. \ref{fig:electronics_plugs_plugged-in}, page \pageref{fig:electronics_plugs_plugged-in}).
%\begin{figure}[hbt]
\begin{figure}[H]
\centering

\caption{Power and USB receptacles}
\label{fig:electronics_plugs}
\end{figure}

%\begin{figure}[hp]
\begin{figure}[H]
\centering
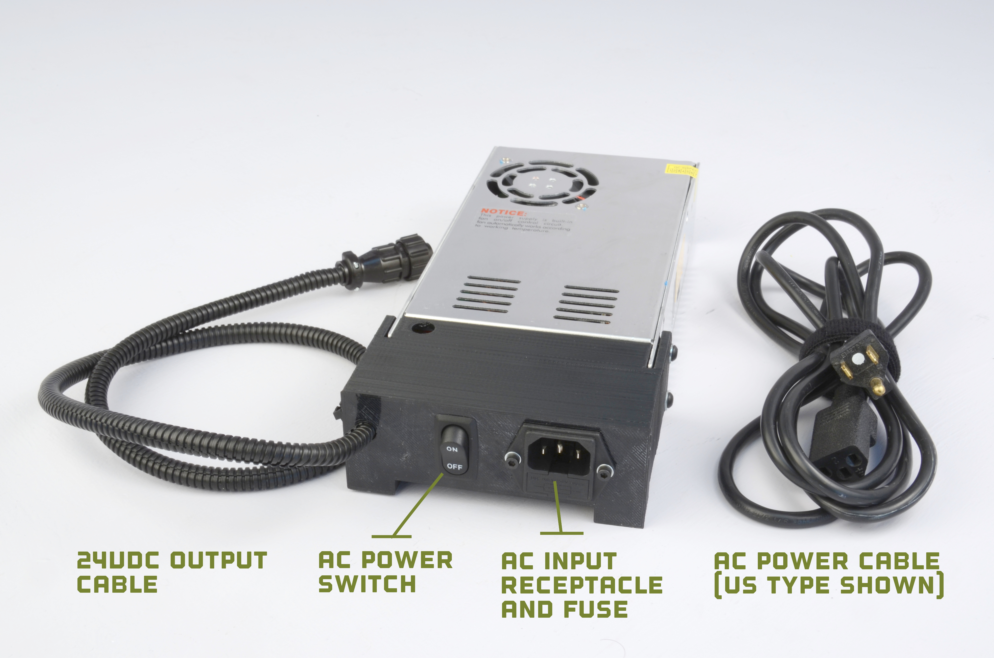
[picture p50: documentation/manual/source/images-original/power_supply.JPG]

\caption{Power supply}
\label{fig:power_supply}
\end{figure}

%\begin{figure}[hp]
\begin{figure}[H]
\centering

\caption{24V DC Power supply plug and receptacle}
\label{fig:ps_plug}
\end{figure}

%\begin{figure}[hp]
\begin{figure}[H]
\centering

\caption{The power supply plug correctly plugged in}
\label{fig:electronics_plugs_plugged-in}
\end{figure}

\item Locate, on the right of the power supply, the red AC voltage switch. Depending on your location you will need to change the AC voltage switch to 115V or 230V. North America is generally 115V and the majority of other regions are 230V. You can find general voltage by country at \texttt{wikipedia.org/wiki/Mains\_electricity\_by\_country}. Make sure that when plugging in the AC power cable it is directly plugged into the wall and \textbf{not} into a power strip. The TAZ 3D printer can potentially pull more current than the power strip will support and may lead to undesirable performance. 

\index{RAMBo}
\item Plug in the USB cable, B plug (smaller square plug) side, into the USB receptacle on the printer electronics. Plug the other end of the USB cable, (larger), into your computer.

\index{PTFE tube}
\item Locate the filament guide with attached PTFE tube
(Fig. \ref{fig:filament_guide}, page \pageref{fig:filament_guide}). The filament guide attaches to the filament guide mount which can be found on the top right side of the printer frame (Fig. \ref{fig:filament_guide_mount}, page \pageref{fig:filament_guide_mount}). The filament guide easily pops on to the guide mount as shown in figure \ref{fig:filament_guide_mount} (pg. \pageref{fig:filament_guide_mount}).
%\begin{figure}[hbt]
\begin{figure}[H]
\centering

\caption{Filament Guide}
\label{fig:filament_guide}
\end{figure}

%\begin{figure}[hbt]
\begin{figure}[H]
\centering

\caption{Filament Guide Mount}
\label{fig:filament_guide_mount}
\end{figure}

%\begin{figure}[hbt]
\begin{figure}[H]
\centering

\caption{Filament Guide Setting}
\label{fig:filament_guide_setting}
\end{figure}

\index{end stops}
\glossary{End stops}{Mechanical or optical switches that are used to mark the 3 home (zero) positions.}
%\begin{figure}[hbt]
\begin{figure}[H]
\centering

\caption{Axes movement directions}
\label{fig:axes_2}
\end{figure}

\begin{figure}[H]
\centering

\caption{End stop locations}
\label{fig:endstops}
\end{figure}

\section{\texttt{ABS \& Acetone Solution Prep}}
Please refer to section \ref{sec:ABS/Acetone Glue} (page \pageref{sec:ABS/Acetone Glue}) for instructions in preparing the ABS/Acetone Glue for use when printing with ABS. As it will take some time to dissolve the ABS into the acetone it may now be a good time to make the solution. If you are printing with PLA, the ABS and Acetone solution is not needed.

\begin{comment}
\index{driver}
\section{Installing Drivers}
Linux and Mac OSX users will not need to install a driver to communicate with the TAZ 3D printer. Windows users will. The drivers can be downloaded from \texttt{LulzBot.com/support/downloads}. A visual guide showing the driver installation process can be found in our download section as well.

\index{pronterface}
\index{printrun}
\index{pronsole}
\index{plater}
\index{stl}
\section{Installing Printrun}
Printrun contains several different applications that can be used to control the TAZ 3D printer. It can be installed on Windows, Mac OSX and Linux based computers. Most users will use Pronterface, the graphical user interface for printrun, when using a host software to interact with the 3D printer. \texttt{Pronsole} allows printing from the command line, and can be used for scripting and some automation. \texttt{Plater} allows you to arrange and combine several STL files into one. More information on the other programs within the Printrun package can be found at \texttt{https://github.com/kliment/Printrun}. Printrun can be downloaded from \texttt{LulzBot.com/support/downloads}. Download the version for your operating system and extract. You will need an archive manager to extract the files. If you do not have one installed we recommend using 7-zip, which can be downloaded for free at \texttt{www.1-zip.org}.

\begin{itemize}
\subsection{Windows Instructions}
\index{Windows}
\item Once downloaded, extract the \texttt{dist} folder to a location of your choice. You can rename the \texttt{dist} folder if you like. Double click \texttt{pronterface.exe} to run Pronterface.

\subsection{Mac OSX Instructions}
\item Once downloaded, extract the \texttt{dist} folder to a location of your choice. Once extracted, double click the \texttt{pronterface-mac-Mar2012.app} file to install.

\subsection{Linux Instructions}
%\begin{itemize}
\item Once downloaded, extract the \texttt{dist} folder to a location of your choice. You will need to ensure that the following dependencies are met. They are listed in the README.md file. You can use this command to install the dependencies: 
\texttt{sudo apt-get install python-serial python-wxgtk2.8 python-pyglet python-tornado python-setuptools python-libxml2 python-gobject python-pip avahi-daemon libavahi-compat-libdnssd1}
followed by:
\texttt{pip install -r requirements.txt}
Open the \texttt{Printrun-source} folder in a terminal and enter the following command:
\texttt{sudo python setup.py install}.
Run Printrun by issuing the following command:
\texttt{python pronterface.py}
\end{itemize}

\index{printrun}
\section{Using Printrun}

%\begin{figure}[hbt]
\begin{figure}[H]
\centering

\caption{Printrun}
\label{fig:printrun}
\end{figure}

Printrun is used to control the printer from a computer. It is divided into 4 main parts: The buttons over the top are used to connect to the printer, load files and start \& stop prints.

The movement controls are on the left hand side, with the G-code preview window in the center and the Log window and Terminal command entry box on the right hand side (Fig. \ref{fig:printrun_labels}, page \pageref{fig:printrun_labels}).

\subsection{Connecting to the TAZ 3D Printer}
To connect to the printer, select the correct port by using the drop down arrow and selecting the active port. The \texttt{Port} button will refresh the Port listing. Once selected choose the default \texttt{115200} buad rate and press \texttt{Connect}. Pronterface will open a connection to the printer and display firmware information in the Log window. If nothing is displayed in the Log window verify you have the correct port and connection speed selected. 

%\begin{figure}[hbt]
\begin{figure}[H]
\centering

\caption{Printrun Functions}
\label{fig:printrun-labels}
\end{figure}

\subsection{Movement} 
%\begin{figure}[hbt]
\begin{figure}[H]
\centering

\caption{Movement Controls}
\label{fig:printrun_controls}
\end{figure}

\subsubsection{Motors off}
The TAZ 3D printer can be moved on all three axes independently. If you would like to do so by hand, use the \texttt{Motors off} button to unlock all the stepper motors. Once unlocked they can be moved by hand. Keep in mind that there is no positional feedback, so if you move an axis you will need to re-home in order to re-establish the hot end's position. 

\subsubsection{mm/min ZY:/ Z:}
These settings control the manual jog speeds when driven with Pronterface. Use caution when changing these figures. Moving the axes too fast can cause the printer to lose steps. If that occurs with the Z axis, it can potentially cause the Z axis to become out of square.

\subsubsection{Homing}
Each axes can be homed either individually or together. Press the \texttt{HomeX} button to move the X axis to the left until it activates the end stop. Once the X axis end stop is activated, the X axis carriage will 'bounce'- it will move over and move back to the home position more slowly. Press the \texttt{HomeY} button to home the Y axis. The Y axis platform will move away from you towards the rear of the printer. Press the \texttt{HomeZ} button to home the Z axis. The Z axis will move down towards the heated bed. Make sure that you home the printer immediately after power up. The printer will not know where the not end is until each axes has been homed. Moving prior to home can be risky since the 3D printer will not know it's initial location.  

\subsubsection{X/Y/Z Axes Movement Controls}
Prior to moving the X, Y or Z axis, make sure that you home each axis. The X, Y and Z axes can be moved utilizing the circular movement controls. Each axis can be moved in either fine moves or large moves, ranging from 0.1mm to 100mm.  For example, to move the \texttt{Y Axis} towards you, move your mouse to the \texttt{+y} section until both the \texttt{+y} and the \texttt{100} is highlighted then select that ring section. To move the \texttt{Y axis} away from you, move your mouse to the \texttt{-y} section until both the \texttt{-y} and the \texttt{100} is highlighted then select that ring section. The X axis can be moved in a similar fashion.

The Z axis movement control operates similarly, but the movement scale is different. The Z axis will move in 0.1mm, 1mm and 10mm increments. The top half of the movement bar will move the Z axis up, by the selected units, while the lower half will move the Z axis down, by the desired units. 
\end{comment}

\end{enumerate}

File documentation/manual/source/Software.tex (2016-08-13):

%
% Software.tex
%
% LulzBot® TAZ User Manual
%
% Copyright (C) 2015 Aleph Objects, Inc.
%
% This document is licensed under the Creative Commons Attribution 4.0
% International Public License (CC BY-SA 4.0) by Aleph Objects, Inc.
%

\section{\texttt{Software Overview}}
\index{software}

To operate your desktop 3D printer you will need to install a few software packages onto your PC. You will need a 3D printer host, an \texttt{.STL} to \texttt{.GCODE} generator, and optional CAD or 3D modeling software.

\texttt{Cura LulzBot\textsuperscript{\miniscule{\textregistered}} Edition is the recommended software for your LulzBot 3D printer.} Download Cura LulzBot Edition by visiting \texttt{LulzBot.com/Cura}.

\glossary{.GCODE}{The file extension for G-Code files}
\glossary{GCODE}{The common name for the most widely used CNC programming language.}
\glossary{CAD}{Computer Aided Design}

\index{GNU/Linux}
\index{OS X}
\index{Windows}
\index{operating system}
All of the following Free/Libre Software packages are available for GNU/Linux, Windows, and OS X. We highly recommend using these programs on GNU/Linux.

\section{\texttt{Software Types}}
\index{Printer Host}
\index{Slicing}
\index{Slicers}
\index{GCODE}
\index{g-code}

\begin{description}
\item{Printer Hosts} \hfill \\
Printer Host software is used to control the 3D printer. The program not only allows you to manually move the printer along all the axes, but set temperatures manually, send commands, and receive feedback/error messages from the onboard electronics. We recommend that new users start with Cura LulzBot\textsuperscript{\miniscule{\textregistered}} Edition as it includes a slicing engine as well.

\item{\texttt{Slicers}} \hfill \\
These programs take the 3-Dimensional model (typically STL/OBJ/etc) and determine the 3D printer toolpath based on the options selected. The slicing engine uses the nozzle diameter, movement speeds, layer height, and other variables to determine the coordinates where it needs to move, and the rates at which it will do so. This information is exported out of the program as a GCODE file. The GCODE file is a plain-text file with a series of text-based codes and a list of the complete X,Y, and Z-axis coordinates used for printing the 3D model. We recommend that new users start with Cura LulzBot Edition as it includes the printer host as well.

%Recommended Slicers:
%\begin{itemize}
%\item Cura LulzBot Edition
%\item Slic3r
%\item Skeinforge
%\item Sfact
%\end{itemize}

\end{description}

\index{download}
\index{driver}
\section{\texttt{Installing Drivers}}
GNU/Linux and OS X users will not need to install a driver to communicate with the LulzBot TAZ 3D printer. Windows users will need to install the drivers. Using Cura LulzBot Edition as your printer host and slicing software is recommended, as the drivers will automatically be installed during the Cura installation process. Download Cura LulzBot Edition by visiting \texttt{LulzBot.com/Cura}. The drivers can also be downloaded from \texttt{LulzBot.com/downloads}. A visual guide showing the driver installation process can be found in our download section as well.

\section{\texttt{CAD and 3D Modeling Software}}
\index{CAD}
\index{software}
\index{STL}

LulzBot is not distributing a CAD or 3D modeling software package. However, multiple Free/Libre Software packages are available. Other common non-free CAD and 3D modeling software are also capable of exporting the required \texttt{.STL} files.

On some CAD and 3D modeling software you will need to select millimeters as the output unit. If possible it is best to build your 3D design in metric units rather than imperial units. Cura requires .STL files sized in millimeters. If an .STL with inches as units is loaded into Cura, the model will be scaled much smaller than expected. You can scale the model by \texttt{25.40} to compensate. The software listed below outputs millimeters as the unit by default.

\subsection{\texttt{FreeCAD}}
\index{FreeCAD}
\index{GNU/Linux}
\index{Windows}
\index{OS X}
Website: \texttt{http://www.freecadweb.org/}

Although still in development, contains a full GUI for building CAD models. FreeCAD is capable of creating simple to complex designs. STL files can also easily be exported for use with 3D printing. FreeCAD is available for GNU/Linux, Windows, and OS X. The latest development version is recommended.

\subsection{\texttt{OpenSCAD}}
\index{OpenSCAD}
\index{GNU/Linux}
\index{Windows}
\index{OS X}
Website: \texttt{http://openscad.org}

OpenSCAD is different than FreeCAD in that it is script based. Rather than using a GUI to generate CAD designs, OpenSCAD CAD designs are created using script based renderings. Users with programming experience would find this useful. Also, OpenSCAD uses a simple script language that is easy for users with little or no programming experience to learn.

\subsection{\texttt{Blender}}
\index{Blender}
\index{GNU/Linux}
\index{Windows}
\index{OS X}
Website: \texttt{http://blender.org}
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

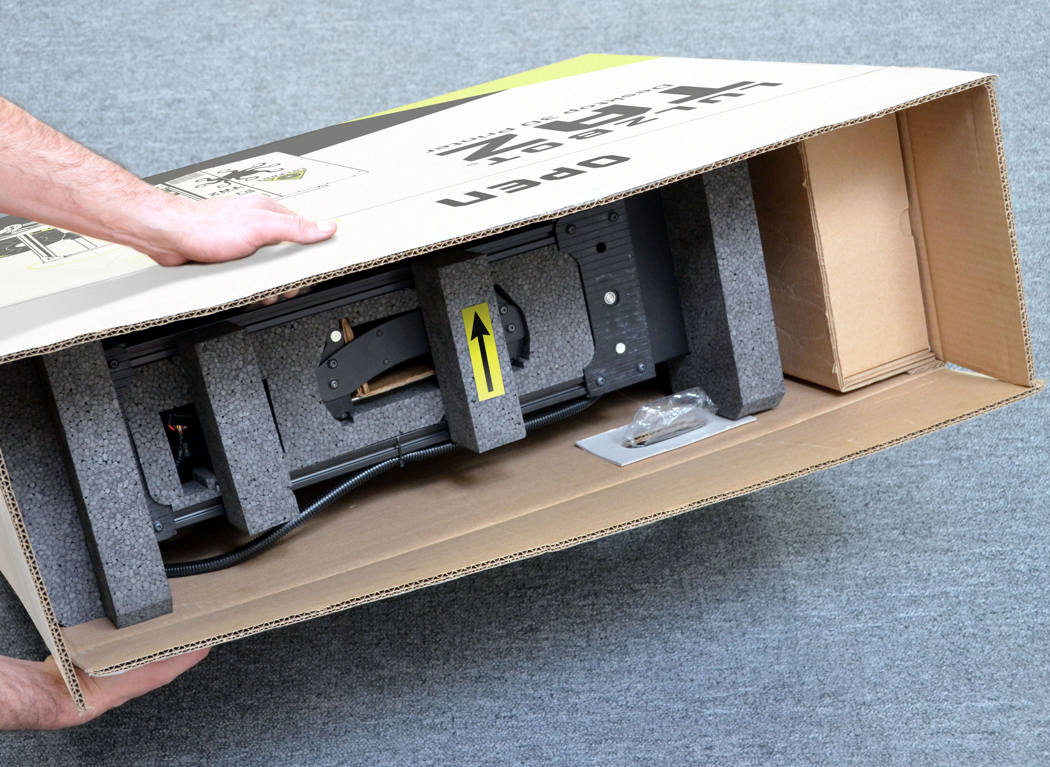
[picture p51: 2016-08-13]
documentation/guide/source/images/lay_box_down.JPG

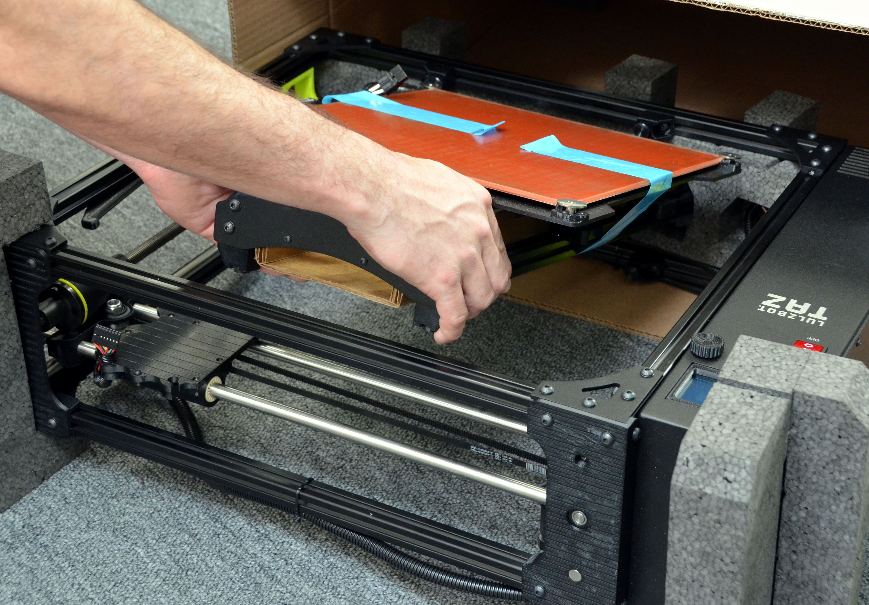
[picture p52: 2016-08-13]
documentation/guide/source/images/lift_out_y-axis_assembly.JPG

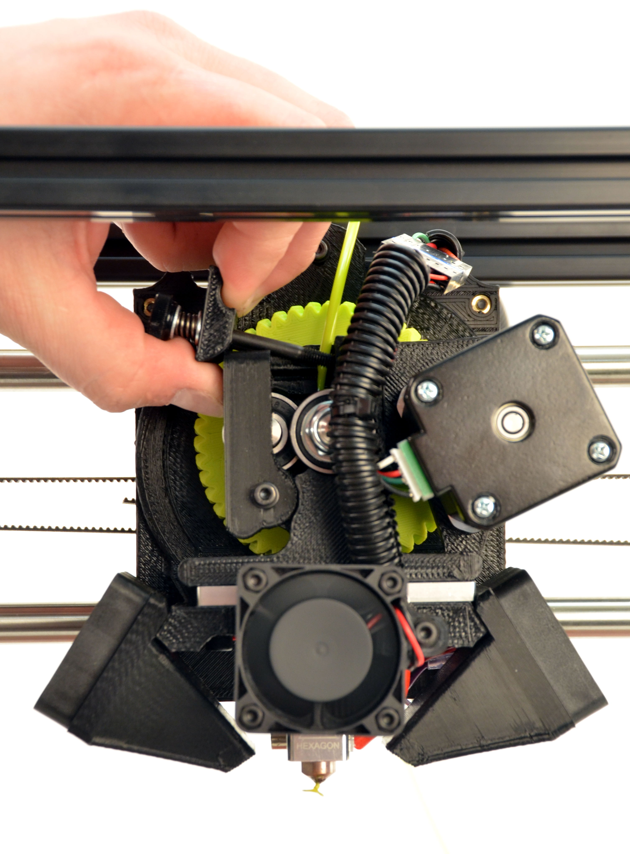
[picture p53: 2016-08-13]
documentation/guide/source/images/close_the_idler_action.JPG

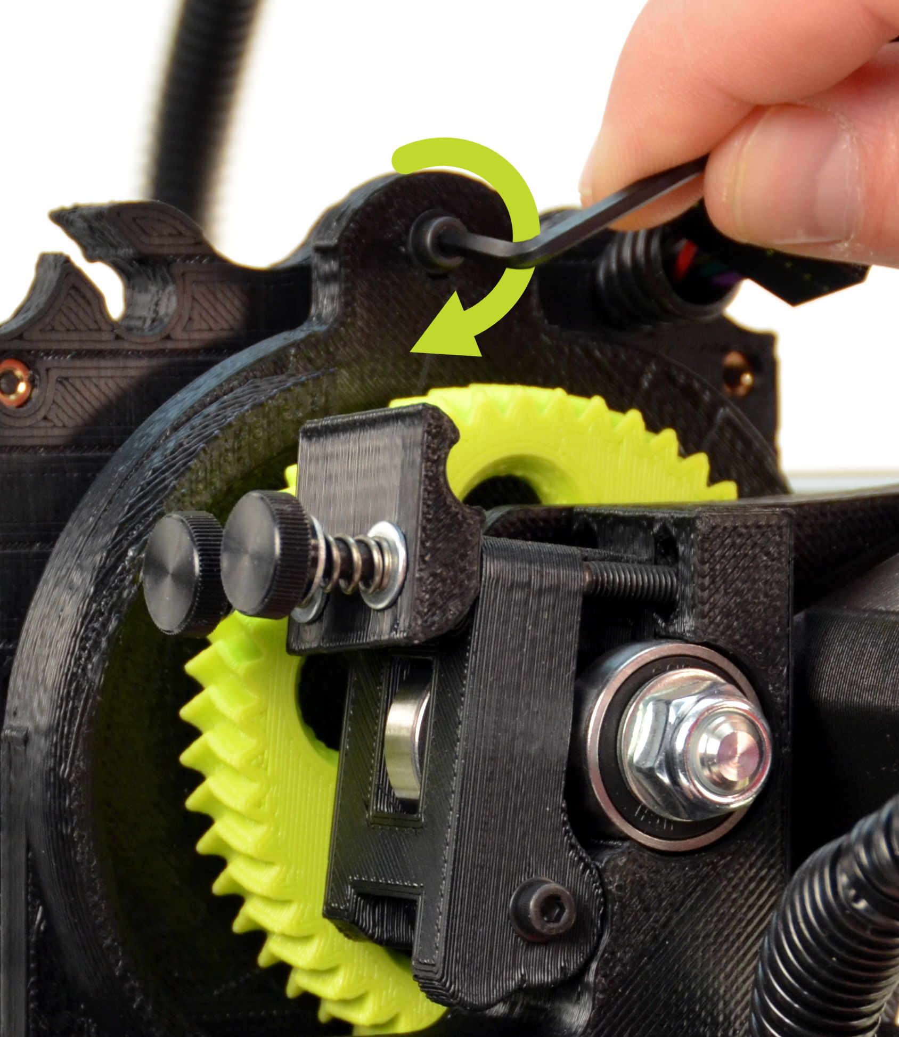
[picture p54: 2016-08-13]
documentation/guide/source/images/HexKeyDetail.JPG

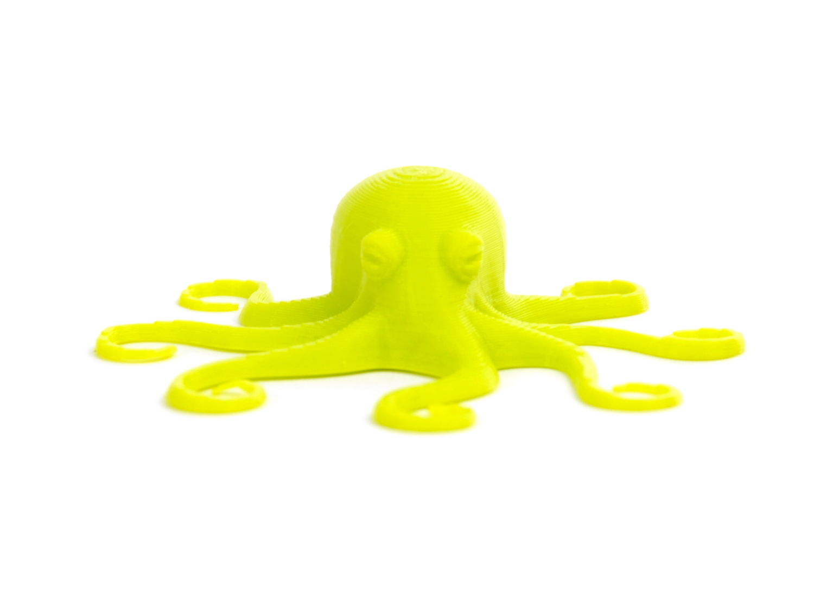
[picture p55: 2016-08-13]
documentation/guide/source/images/TAZ_6_Octopus.JPG

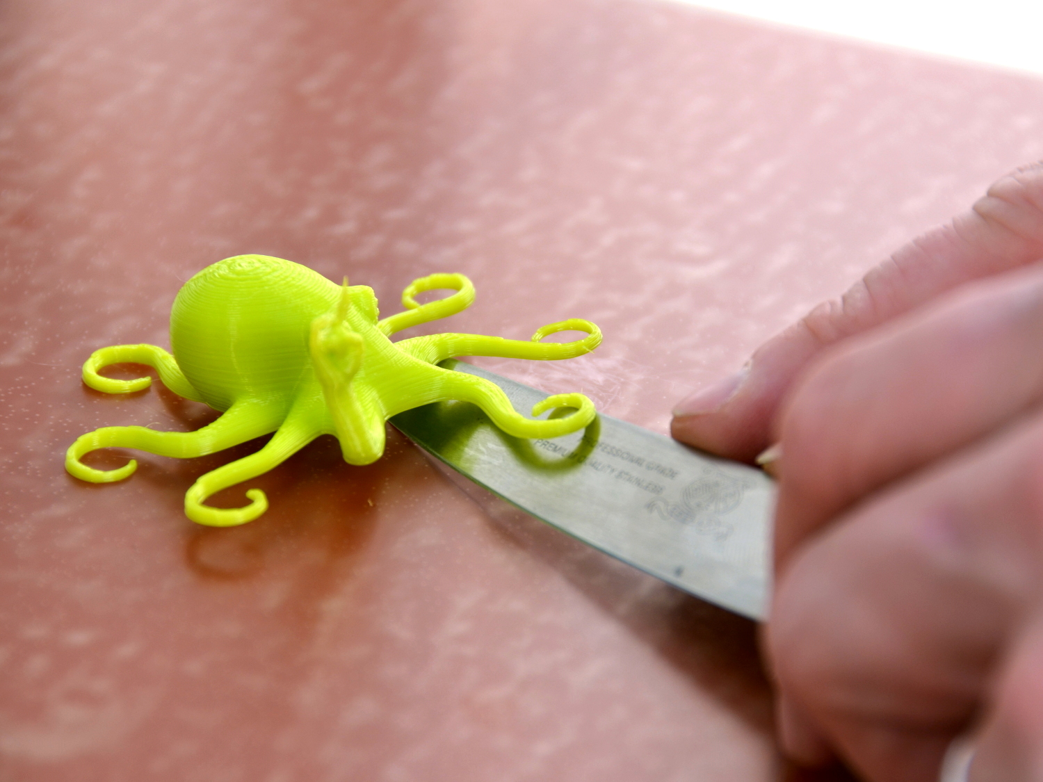
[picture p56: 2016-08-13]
documentation/guide/source/images/TAZ_6_PrintRemoval_third.JPG

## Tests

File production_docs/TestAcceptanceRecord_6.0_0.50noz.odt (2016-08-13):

Model: LulzBot TAZ 6 3D Printer

Serial Number:

Heat Bed Batch #:

Date Completed:

Completed by:

Configuration:

Electronics: RAMBo 1.3L

Firmware: Marlin Version 1.0.2.19

Nozzle: LulzBot v2 Hot End with 0.50mm nozzle

Settings:

Part | Steps/mm | Max length | Micro step mode | Digipot
X Motor | 100.5 | 298 | 16 | 175
Y Motor | 100.5 | 275 | 16 | 175
Z Motor | 1600 | 250 | 16 | 240
E0 Motor | | NA | 16 | 135

Z Offset:

General

- Are all the screws and zip ties tight?
- Are the X and Y axis square to each other?
- Are the gaps at the ends of the extrusion closed?
- Are all the parts flush and straight to the edges with clean lines?
- Is the t-nut for the second extruder installed correctly?
- Does the SD card slide in and out of the slot freely?
- Are the current version of parts being used?
- Verify that the following are mounted correctly:
    1. Filament guide tube, tube on back side of mount
    2. Spool Arm, correct height
    3. Idler retainer, taller side on left
- Are the switches tight? They shouldn't wiggle side to side.
- Are all 11 rubber feet installed?
- Is the PEI print surface free of bubbles and wrinkles?
- Is the heat bed adhesive smooth and consistent?
- Does filament slide through the filament guide tube?

Y-Axis

- Does the print bed move freely back and forth?
- Is the Y-axis tight side to side from motion and twisting?
- Are all the screws on the bearing holders tight?
- Does the Y belt rub the bottom of the y-idler by the bearings?
- Is one of the set screws on the Y pulley aligned with the flat on the motor shaft?
- Are both pulley set screws tightened?
- Is the level of the Y pulley at the same height as where the belt mounts on the belt holder?
- Is the Y belt tight?
- Are all the Y mounting brackets flush and tight?
- Are the belts trimmed far enough to not interfere with the pulley or bearing?
- Are the plastic parts flush to the top of the y end plate?

X-Axis

- Is one of the set screws on the X pulley aligned with the flat on the motor shaft?
- Are both pulley set screws tightened?
- Is the belt free from rubbing anywhere during motion?
- Is the X belt tight?
- Does the X-axis move freely end to end?
- Are the X bars flush with the outside for the X-end idler (right side)?
- Are the set screws that hold the X bars tight?
- Are the belts trimmed far enough to not interfere with the pulley or bearing?
- Is the X-axis level and parallel to the bed?

Z-Axis

- Do the lead screws rotate smoothly with no up and down movement between the bearings?
- Are the four Z coupler set screws tight and aligned with flats on the drive rods and motors?
- Are the Z smooth rods flush with the top plate?

Tool Head

- Can you adjust the extruder springs?
- Are the herringbone grooves on the extruder gears lined up?
- Is the extruder mount secure on the X carriage?
- Are the extrusion fans mounted correctly?
- Is the heat sink fan mounted correctly?
- Does the idler bearing stick out of the idler block?
- Is the hobbing aligned to the hole in the extruder?
- Is the set screw in the small gear tight and on the flat of the motor shaft?
- Can you feed filament about 100mm from the top of the extruder?
- Are the gears tight with no back-lash?
- Do the extruder gears turn smoothly for several rotations?

Electronics

- Are the screws that fasten the control box to the frame tight?
- Can you plug in USB cable from the outside of the enclosure?
- Is the plug cover for second extruder installed with the strap attached to the lower right screw?
- Has the protective plastic been removed from LCD?
- Has the protective cover been removed from the clear polycarb LCD cover?
- Is the LCD secured in place firmly?
- Is the LCD knob tightly secured to the LCD?

Test and Verification Results:

- LCD functions normally.
- Belts aligned on bearings and properly tensioned.
- Verify case fan is spinning freely.
- Verify the heat sink fan is running.
- Verify you can run the extrusion fans.
- Hexagon Hot End temperature control verified.
- Extruder calibration verified. Check that EEPROM values are correct.
- Z offset calibrated and verified.
- Bed level consistent across bed.
- X, Y and Z stop switches verified.
- Flat of the nozzle contacts all four bed corners.
- Wipe sequence is in center of wiper pad
- Bed temperature control verified.
- Cables secure and free of interference/contact with table motion.
- Cable connectors fully engaged and oriented correctly.
- Bearing conditioning (burn in) complete.
- X, Y and Z motion smooth over range and speeds.
- Test print (Octopus) successful.
- Loctite® applied to all pulley and coupler set screws.

Test/Acceptance Record

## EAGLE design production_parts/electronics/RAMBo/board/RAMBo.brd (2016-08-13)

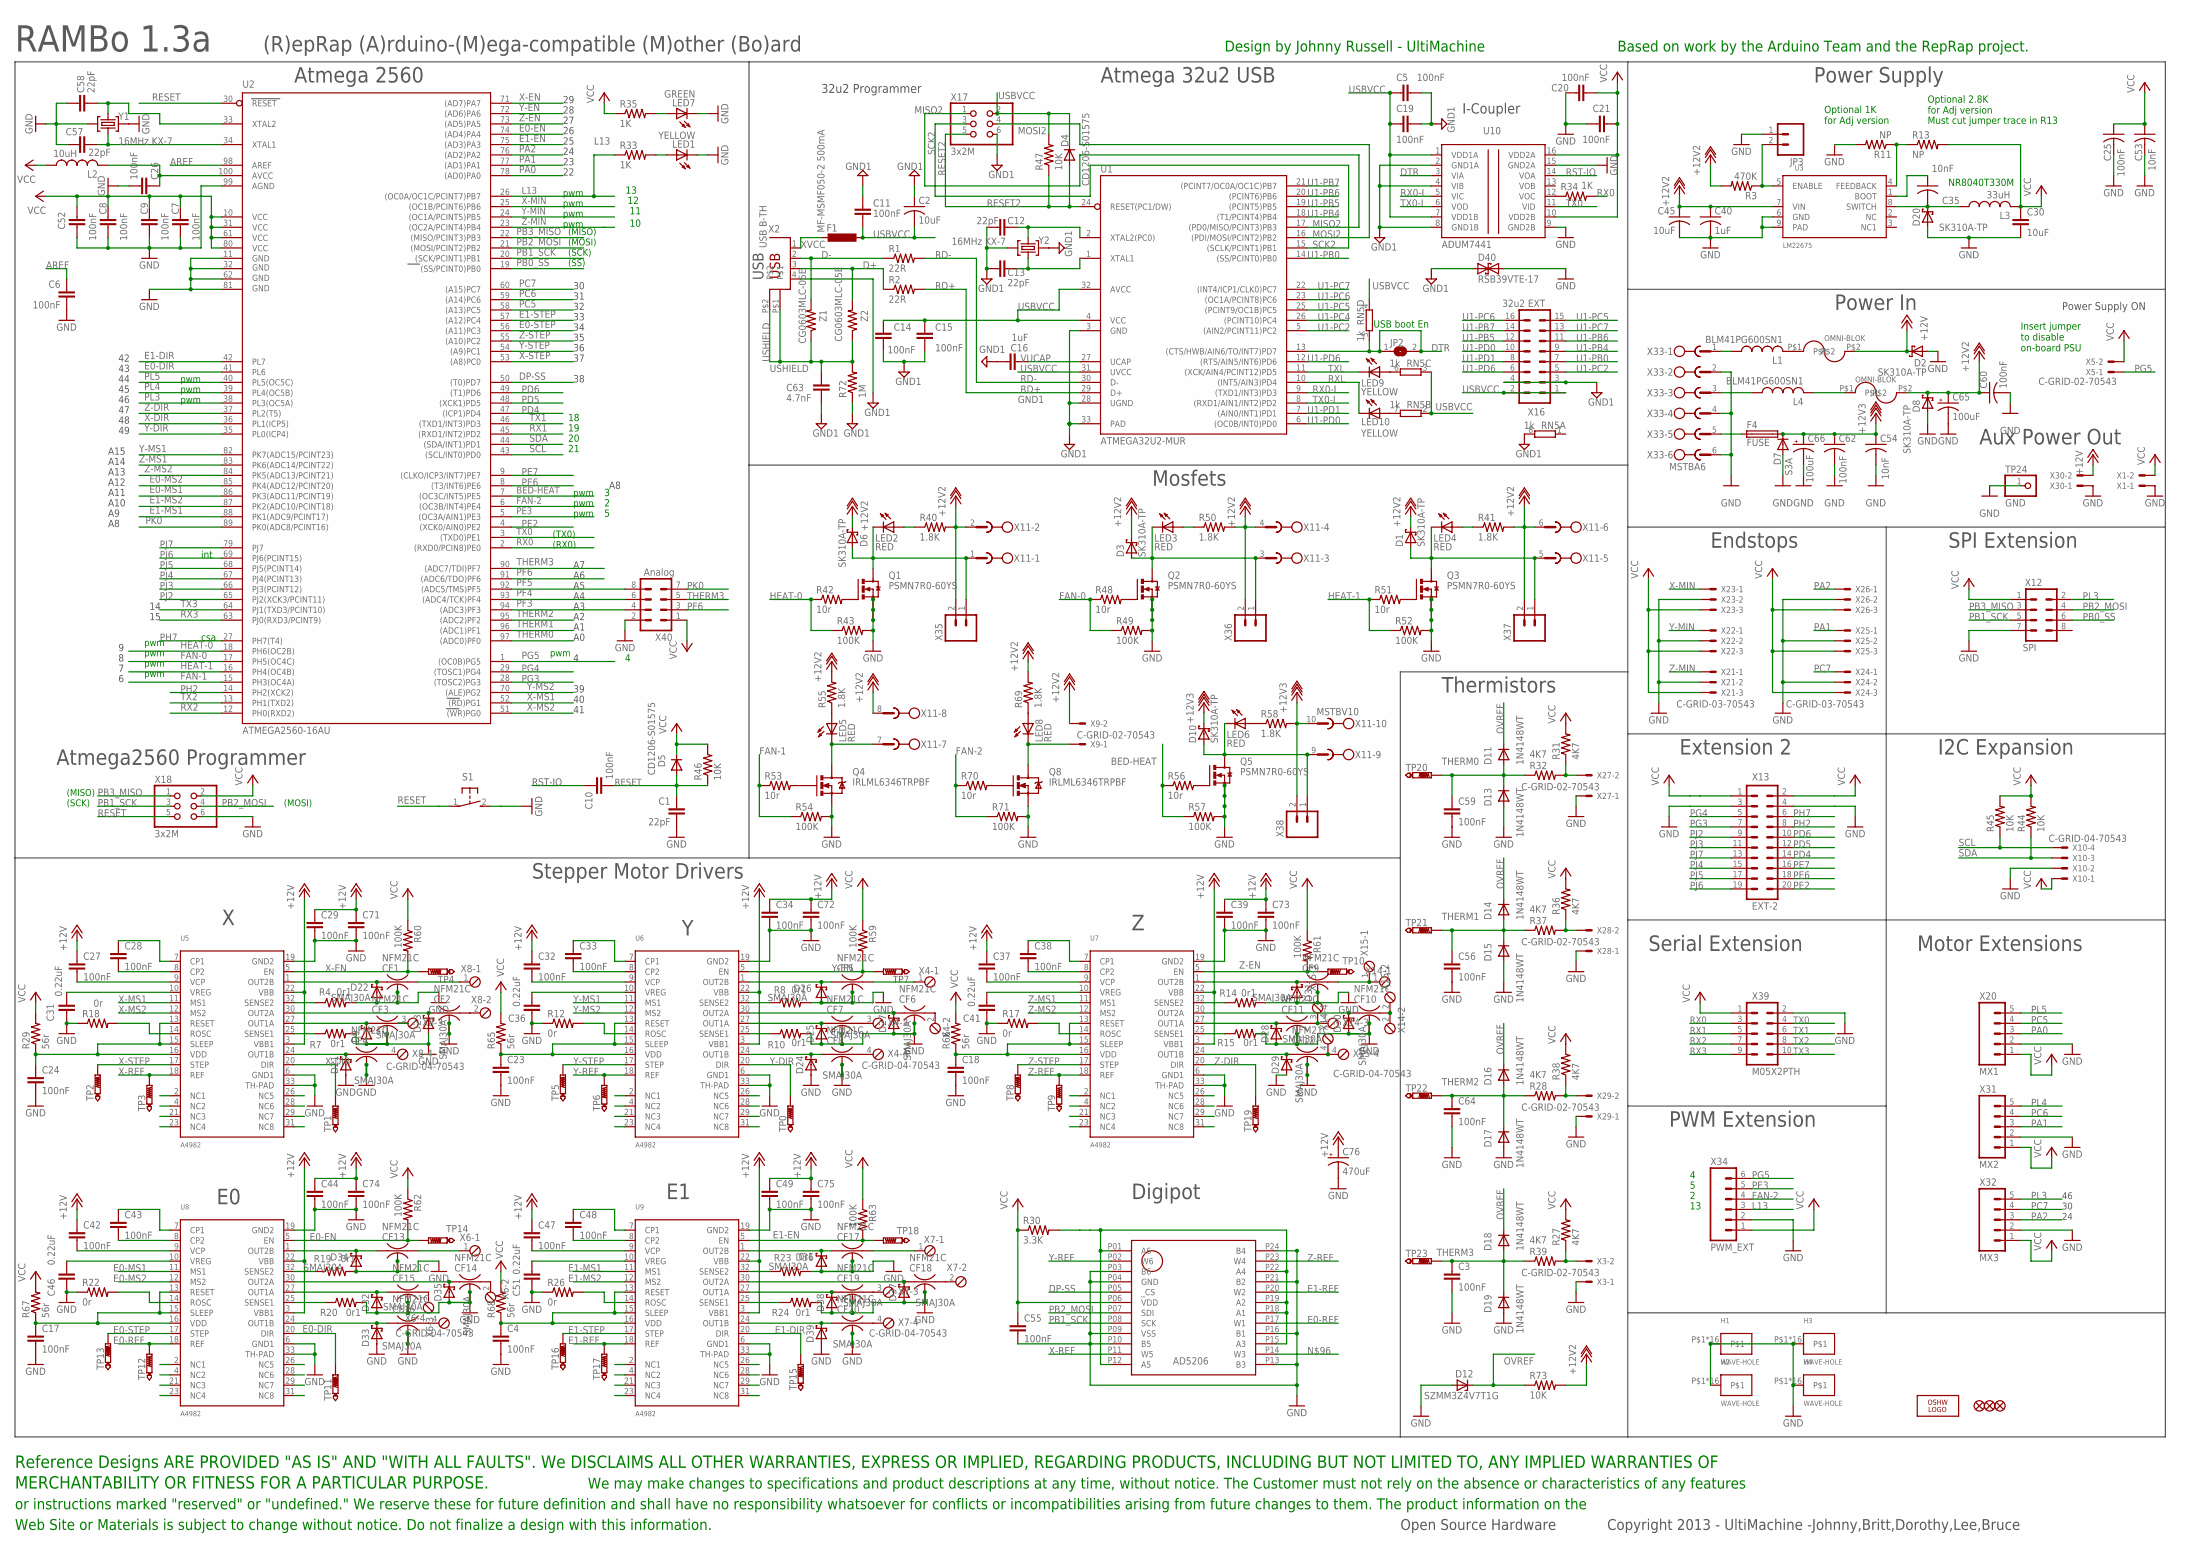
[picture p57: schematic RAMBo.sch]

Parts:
C1, C12, C13, C57, C58: 22pF; C0603
C2: 10uF; C0805
C3, C4, C6, C7, C8, C9, C10, C11, C14, C15, C17, C18, C23, C24, C25, C26, C27, C28, C29, C32, C33, C34, C37, C38, C39, C42, C43, C44, C47, C48, C49, C52, C55, C56, C59, C60, C62, C64, C71, C72, C73, C74, C75: 100nF; C0603
C5, C19, C20, C21: 100nF; C0402
C16: 1uF; C0603
C30: 10uF; C1210K
C31, C36, C41, C46, C51: 0.22uF; C0603
C35, C53, C54: 10nF; C0603
C40: 1uF; C0805
C45: 10uF; C2220K
C63: 4.7nF; C0402
C65, C66: 100uF; E3,5-8
C76: 470uF; C12,5-5
CF1, CF2, CF3, CF4, CF5, CF6, CF7, CF8, CF9, CF10, CF11, CF12, CF13, CF14, CF15, CF16, CF17, CF18, CF19, CF20: NFM21C
D1, D2, D3, D6, D8, D10, D20: SK310A-TP; SMA-SM
D4, D5: CD1206-S01575; MINIMELF
D7: S3A; DO-214AB
D9, D21, D22, D23, D24, D25, D26, D27, D28, D29, D30, D31, D32, D33, D34, D35, D36, D37, D38, D39: SMAJ30A; SMA-SM
D11, D13, D14, D15, D16, D17, D18, D19: 1N4148WT; SOD523
D12: SZMM3Z4V7T1G; SOD323-R
D40: RSB39VTE-17; SOD323-R
F1: MF-MSMF050-2 500mA; L1812
F2, F3: OMNI-BLOK
F4: FUSE; FUSE-ATO-SMD
FID1, FID2, FID3: FIDUCIAL1X2.5; FIDUCIAL-1X2.5
H1, H2, H3, H4: WAVE-HOLE; 3,0-WAVE-HOLE
JP2: SJ
JP3: M02PTH; 1X02
L1, L4: BLM41PG600SN1; L1806
L2: 10uH; C0805
L3: 33uH; NR8040
LED1, LED9, LED10: YELLOW; CHIP-LED0805
LED2, LED3, LED4, LED5, LED6, LED8: RED; CHIP-LED0805
LED7: GREEN; CHIP-LED0805
LOGO1: OSHW_LOGO_8MILX0150-NT; OSHW_8X150_NOTEXT
Q1, Q2, Q3, Q5: PSMN7R0-60YS; SOT669
Q4, Q8: IRLML6346TRPBF; SOT23-3
R1, R2: 22R; R0402
R3: 470K; R0603
R4, R7, R8, R10, R14, R15, R19, R20, R23, R24: 0r1; R1206
R11, R13: NP; R0603
R12, R17, R18, R22, R26: 0r; R0603
R27, R28, R31, R32, R36, R37, R38, R39: 4K7; R0603
R29, R65, R66, R67, R68: 56r; R0603
R30: 3.3K; R0603
R33, R34, R35: 1K; R0603
R40, R41, R50, R55, R58, R69: 1.8K; R0603
R42, R48, R51, R53, R56, R70: 10r; R0603
R43, R49, R52, R54, R57, R59, R60, R61, R62, R63, R71: 100K; R0603
R44, R45, R46, R47, R73: 10K; R0603
R72: 1M; R0402
RN5: 1k; CAY16
S1: 31-XX; B3F-31XX
TP0, TP1, TP2, TP3, TP4, TP5, TP6, TP7, TP8, TP9, TP10, TP11, TP12, TP13, TP14, TP15, TP16, TP17, TP18, TP19: PTR1B1,27TH; B1,27TH
TP20, TP21, TP22, TP23: PTR1B1,27; B1,27
TP24: GND; 1X01
U1: ATMEGA32U2-MUR; QFN32TROUND
U2: ATMEGA2560-16AU; TQFP100
U3: LM22675; SOIC127P600X170-9N
U4: AD5206; TSSOP24
U5, U6, U7, U8, U9: A4982; QFN32TROUND
U10: ADUM7441; QSOP16
X1, X3, X5, X9, X27, X28, X29, X30: C-GRID-02-70543; 70543-02
X2: USB B-TH; PN61729
X4, X6, X7, X8, X14, X15: C-GRID-04-70543; 4POL254
X10: C-GRID-04-70543; 70543-04
X11: MSTBV10
X12: SPI; 2X4
X13: EXT-2; 2X10
X16: 32u2 EXT; 2X8
X17, X18: 3x2M; 2X03
X20: MX1; 1X05
X21, X22, X23, X24, X25, X26: C-GRID-03-70543; 70543-03
X31: MX2; 1X05
X32: MX3; 1X05
X33: MSTBA6
X34: PWM_EXT; 1X06
X35, X36, X37, X38: M02PTH; 1X02
X39: M05X2PTH; AVR_ICSP
X40: Analog; 2X4
Y1, Y2: 16MHz KX-7; CRYSTAL-3.2-2.5
Z1, Z2: CG0603MLC-05E; R0603

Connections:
+12V: C27.1, C29.1, C32.1, C34.1, C37.1, C39.1, C42.1, C44.1, C47.1, C49.1, C71.1, C72.1, C73.1, C74.1, C75.1, C76.+, D2.C, F2.P$2, U5.3 (VBB1), U5.22 (VBB), U6.3 (VBB1), U6.22 (VBB), U7.3 (VBB1), U7.22 (VBB), U8.3 (VBB1), U8.22 (VBB), U9.3 (VBB1), U9.22 (VBB), X30.2
+12V2: C40.1, C45.1, C60.1, C65.+, D1.C, D3.C, D6.C, D8.C, F3.P$2, R3.2, R40.2, R41.2, R50.2, R55.2, R69.2, R73.2, U3.7 (VIN), X9.2, X11.2, X11.4, X11.6, X11.8, X35.2, X36.2, X37.2
+12V3: C54.1, C62.1, C66.+, D7.C, D10.C, F4.P$2 (2), R58.2, X11.10, X38.2
AREF: C6.1, U2.98 (AREF)
BED-HEAT: R56.1, R57.1, U2.7 ((OC3C/INT5)PE5)
D+: R2.1, X2.3, Z2.2
D-: R1.1, X2.2, Z1.2
DP-SS: U2.50 ((T0)PD7), U4.P05 (_CS)
DTR: JP2.1, JP2.2, RN5.5 (2), U1.13 ((CTS/HWB/AIN6/TO/INT7)PD7), U10.3 (VIA)
E0-DIR: TP11.TP, U2.41 (PL6), U8.20 (DIR)
E0-EN: R62.2, TP14.TP, U2.74 ((AD4)PA4), U8.5 (EN)
E0-MS1: U2.86 (PK3(ADC11/PCINT19)), U8.11 (MS1)
E0-MS2: U2.85 (PK4(ADC12/PCINT20)), U8.12 (MS2)
E0-REF: TP12.TP, U4.P17 (W1), U8.18 (REF)
E0-STEP: TP13.TP, U2.56 ((A11)PC3), U8.17 (STEP)
E1-DIR: TP15.TP, U2.42 (PL7), U9.20 (DIR)
E1-EN: R63.2, TP18.TP, U2.75 ((AD3)PA3), U9.5 (EN)
E1-MS1: U2.88 (PK1(ADC9/PCINT17)), U9.11 (MS1)
E1-MS2: U2.87 (PK2(ADC10/PCINT18)), U9.12 (MS2)
E1-REF: TP17.TP, U4.P20 (W2), U9.18 (REF)
E1-STEP: TP16.TP, U2.57 ((A12)PC4), U9.17 (STEP)
FAN-0: R48.1, R49.1, U2.17 (PH5(OC4C))
FAN-1: R53.1, R54.1, U2.15 (PH3(OC4A))
FAN-2: R70.1, R71.1, U2.6 ((OC3B/INT4)PE4), X34.4
GND: C1.2, C3.2, C4.2, C6.2, C7.2, C8.2, C9.2, C17.2, C18.2, C20.2, C21.1, C23.2, C24.2, C25.2, C26.2, C29.2, C30.2, C31.1, C34.2, C36.1, C39.2, C40.2, C41.1, C44.2, C45.2, C46.1, C49.2, C51.1, C52.2, C53.2, C54.2, C55.2, C56.2, C57.2, C58.2, C59.2, C60.2, C62.2, C64.2, C65.-, C66.-, C71.2, C72.2, C73.2, C74.2, C75.2, C76.-, CF1.2@1 (2), CF1.2@2 (2), CF2.2@1 (2), CF2.2@2 (2), CF3.2@1 (2), CF3.2@2 (2), CF4.2@1 (2), CF4.2@2 (2), CF5.2@1 (2), CF5.2@2 (2), CF6.2@1 (2), CF6.2@2 (2), CF7.2@1 (2), CF7.2@2 (2), CF8.2@1 (2), CF8.2@2 (2), CF9.2@1 (2), CF9.2@2 (2), CF10.2@1 (2), CF10.2@2 (2), CF11.2@1 (2), CF11.2@2 (2), CF12.2@1 (2), CF12.2@2 (2), CF13.2@1 (2), CF13.2@2 (2), CF14.2@1 (2), CF14.2@2 (2), CF15.2@1 (2), CF15.2@2 (2), CF16.2@1 (2), CF16.2@2 (2), CF17.2@1 (2), CF17.2@2 (2), CF18.2@1 (2), CF18.2@2 (2), CF19.2@1 (2), CF19.2@2 (2), CF20.2@1 (2), CF20.2@2 (2), D2.A, D7.A, D8.A, D9.A, D12.A, D13.A, D15.A, D17.A, D19.A, D20.A, D21.A, D22.A, D23.A, D24.A, D25.A, D26.A, D27.A, D28.A, D29.A, D30.A, D31.A, D32.A, D33.A, D34.A, D35.A, D36.A, D37.A, D38.A, D39.A, D40.C (2), H1.P$1, H1.P$2, H1.P$3, H1.P$4, H1.P$5, H1.P$6, H1.P$7, H1.P$8, H1.P$17, H1.P$18, H1.P$19, H1.P$20, H1.P$21, H1.P$22, H1.P$23, H1.P$24, H2.P$1, H2.P$2, H2.P$3, H2.P$4, H2.P$5, H2.P$6, H2.P$7, H2.P$8, H2.P$17, H2.P$18, H2.P$19, H2.P$20, H2.P$21, H2.P$22, H2.P$23, H2.P$24, H3.P$1, H3.P$2, H3.P$3, H3.P$4, H3.P$5, H3.P$6, H3.P$7, H3.P$8, H3.P$17, H3.P$18, H3.P$19, H3.P$20, H3.P$21, H3.P$22, H3.P$23, H3.P$24, H4.P$1, H4.P$2, H4.P$3, H4.P$4, H4.P$5, H4.P$6, H4.P$7, H4.P$8, H4.P$17, H4.P$18, H4.P$19, H4.P$20, H4.P$21, H4.P$22, H4.P$23, H4.P$24, JP3.1, LED1.C, LED7.C, Q1.1 (S), Q1.2 (S), Q1.3 (S), Q2.1 (S), Q2.2 (S), Q2.3 (S), Q3.1 (S), Q3.2 (S), Q3.3 (S), Q4.2 (S), Q5.1 (S), Q5.2 (S), Q5.3 (S), Q8.2 (S), R4.2, R7.2, R8.2, R10.2, R11.2, R12.1, R14.2, R15.2, R17.1, R18.1, R19.2, R20.2, R22.1, R23.2, R24.2, R26.1, R43.2, R49.2, R52.2, R54.2, R57.2, R71.2, S1.2 (S), TP24.1, U2.11 (GND), U2.32 (GND1), U2.62 (GND2), U2.81 (GND3), U2.99 (AGND), U3.6 (GND), U3.9 (PAD), U4.P03 (B6), U4.P04 (GND), U4.P09 (VSS), U4.P10 (B5), U4.P13 (B3), U4.P16 (B1), U4.P21 (B2), U4.P24 (B4), U5.6 (GND1), U5.19 (GND2), U5.33 (TH-PAD), U6.6 (GND1), U6.19 (GND2), U6.33 (TH-PAD), U7.6 (GND1), U7.19 (GND2), U7.33 (TH-PAD), U8.6 (GND1), U8.19 (GND2), U8.33 (TH-PAD), U9.6 (GND1), U9.19 (GND2), U9.33 (TH-PAD), U10.9 (GND2B), U10.15 (GND2A), X1.1, X3.1, X10.2, X12.7, X13.3, X13.4, X18.6, X20.2, X21.2, X22.2, X23.2, X24.2, X25.2, X26.2, X27.1, X28.1, X29.1, X30.1, X31.2, X32.2, X33.2, X33.4, X33.6, X34.2, X39.2, X40.2, Y1.2 (GND), Y1.4 (GND)
GND1: C2.1, C5.2, C11.2, C12.2, C13.2, C14.2, C15.2, C16.2, C19.2, C63.2, D40.A (1), R72.1, RN5.8 (2), U1.3 (GND), U1.28 (UGND), U1.33 (PAD), U10.2 (GND1A), U10.4 (VIB), U10.8 (GND1B), X2.4, X16.3, X16.4, X17.6, Y2.2 (GND), Y2.4 (GND)
HEAT-0: R42.1, R43.1, U2.18 (PH6(OC2B))
HEAT-1: R51.1, R52.1, U2.16 (PH4(OC4B))
L13: R33.1, U2.26 ((OC0A/OC1C/PCINT7)PB7), X34.3
MISO2: U1.17 ((PD0/MISO/PCINT3)PB3), X17.1
MOSI2: U1.16 ((PDI/MOSI/PCINT2)PB2), X17.4
unnamed: C31.2, U5.10 (VREG)
unnamed: LED1.A, R33.2
unnamed: LED7.A, R35.2
unnamed: R8.1, U6.32 (SENSE2)
unnamed: R10.1, U6.25 (SENSE1)
unnamed: C33.2, U6.8 (CP2)
unnamed: C32.2, U6.9 (VCP)
unnamed: C36.2, U6.10 (VREG)
unnamed: R12.2, U6.14 (ROSC)
unnamed: Q4.1 (G), R53.2
unnamed: LED10.A, RN5.7 (2)
unnamed: C24.1, R29.1, U5.13 (RESET), U5.15 (SLEEP), U5.16 (VDD)
unnamed: L1.P$1 (1), X33.1
unnamed: F3.P$1, L4.P$2 (2)
unnamed: JP3.2, R3.1, U3.5 (ENABLE)
unnamed: F4.P$1 (1), X33.5
unnamed: CF5.1, D26.C, U6.1 (OUT2B)
unnamed: CF20.3, X7.4
unnamed: CF5.3, X4.1
unnamed: CF6.1, D27.C, U6.30 (OUT2A)
unnamed: D6.A, LED2.C, Q1.MB (D), X11.1, X35.1
unnamed: R4.1, U5.32 (SENSE2)
unnamed: CF7.1, D25.C, U6.27 (OUT1A)
unnamed: C33.1, U6.7 (CP1)
unnamed: C23.1, R65.1, U6.13 (RESET), U6.15 (SLEEP), U6.16 (VDD)
unnamed: Q2.4 (G), R48.2
unnamed: C26.1, L2.2, U2.100 (AVCC)
unnamed: R14.1, U7.32 (SENSE2)
unnamed: R15.1, U7.25 (SENSE1)
unnamed: C38.2, U7.8 (CP2)
unnamed: C37.2, U7.9 (VCP)
unnamed: C41.2, U7.10 (VREG)
unnamed: R17.2, U7.14 (ROSC)
unnamed: CF10.1, D30.C, U7.30 (OUT2A)
unnamed: CF11.1, D28.C, U7.27 (OUT1A)
unnamed: R7.1, U5.25 (SENSE1)
unnamed: C28.2, U5.8 (CP2)
unnamed: C27.2, U5.9 (VCP)
unnamed: CF19.3, X7.3
unnamed: CF12.1, D29.C, U7.24 (OUT1B)
unnamed: CF12.3, X14.4, X15.4
unnamed: C38.1, U7.7 (CP1)
unnamed: R18.2, U5.14 (ROSC)
unnamed: C18.1, R66.1, U7.13 (RESET), U7.15 (SLEEP), U7.16 (VDD)
unnamed: LED8.C, Q8.3 (D), X9.1
unnamed: R19.1, U8.32 (SENSE2)
unnamed: CF1.1, D22.C, U5.1 (OUT2B)
unnamed: C28.1, U5.7 (CP1)
unnamed: R20.1, U8.25 (SENSE1)
unnamed: C43.2, U8.8 (CP2)
unnamed: CF3.1, D9.C, U5.27 (OUT1A)
unnamed: CF4.1, D21.C, U5.24 (OUT1B)
unnamed: LED9.A, RN5.6 (2)
unnamed: R34.1, U10.12 (VOC)
unnamed: C42.2, U8.9 (VCP)
unnamed: C46.2, U8.10 (VREG)
unnamed: R22.2, U8.14 (ROSC)
unnamed: CF13.1, D34.C, U8.1 (OUT2B)
unnamed: CF13.3, X6.1
unnamed: CF14.1, D35.C, U8.30 (OUT2A)
unnamed: CF15.1, D32.C, U8.27 (OUT1A)
unnamed: C43.1, U8.7 (CP1)
unnamed: C17.1, R67.1, U8.13 (RESET), U8.15 (SLEEP), U8.16 (VDD)
unnamed: CF18.3, X7.2
unnamed: R23.1, U9.32 (SENSE2)
unnamed: R24.1, U9.25 (SENSE1)
unnamed: C48.2, U9.8 (CP2)
unnamed: C47.2, U9.9 (VCP)
unnamed: C51.2, U9.10 (VREG)
unnamed: R26.2, U9.14 (ROSC)
unnamed: CF20.1, D39.C, U9.24 (OUT1B)
unnamed: CF19.1, D38.C, U9.27 (OUT1A)
unnamed: CF17.1, D36.C, U9.1 (OUT2B)
unnamed: CF18.1, D37.C, U9.30 (OUT2A)
unnamed: C48.1, U9.7 (CP1)
unnamed: C4.1, R68.1, U9.13 (RESET), U9.15 (SLEEP), U9.16 (VDD)
unnamed: LED8.A, R69.1
unnamed: Q8.1 (G), R70.2
unnamed: LED2.A, R40.1
unnamed: R30.2, U4.P01 (A6), U4.P12 (A5), U4.P15 (A3), U4.P18 (A1), U4.P19 (A2), U4.P22 (A4)
unnamed: R31.1, R32.2, X27.2
unnamed: Q1.4 (G), R42.2
unnamed: R36.1, R37.2, X28.2
unnamed: Q3.4 (G), R51.2
unnamed: R28.2, R38.1, X29.2
unnamed: Q5.4 (G), R56.2
unnamed: CF17.3, X7.1
unnamed: CF16.3, X6.4
unnamed: CF15.3, X6.3
unnamed: D3.A, LED3.C, Q2.MB (D), X11.3, X36.1
unnamed: LED3.A, R50.1
unnamed: D1.A, LED4.C, Q3.MB (D), X11.5, X37.1
unnamed: LED4.A, R41.1
unnamed: LED5.C, Q4.3 (D), X11.7
unnamed: LED5.A, R55.1
unnamed: D10.A, LED6.C, Q5.MB (D), X11.9, X38.1
unnamed: LED6.A, R58.1
unnamed: CF14.3, X6.2
unnamed: CF16.1, D33.C, U8.24 (OUT1B)
unnamed: CF4.3, X8.4
unnamed: CF3.3, X8.3
unnamed: R27.1, R39.2, X3.2
unnamed: CF2.3, X8.2
unnamed: C35.1, U3.1 (BOOT)
unnamed: CF1.3, X8.1
unnamed: CF8.3, X4.4
unnamed: CF7.3, X4.3
unnamed: R11.1, R13.1, U3.4 (FEEDBACK)
unnamed: C35.2, D20.C, L3.P$1 (1), U3.8 (SWITCH)
unnamed: CF6.3, X4.2
unnamed: CF8.1, D24.C, U6.24 (OUT1B)
unnamed: CF9.1, D31.C, U7.1 (OUT2B)
unnamed: CF11.3, X14.3, X15.3
unnamed: CF9.3, X14.1, X15.1
unnamed: CF10.3, X14.2, X15.2
unnamed: F2.P$1, L1.P$2 (2)
unnamed: CF2.1, D23.C, U5.30 (OUT2A)
unnamed: L4.P$1 (1), X33.3
OVREF: D11.C, D12.C, D14.C, D16.C, D18.C, R73.1
PA0: U2.78 ((AD0)PA0), X20.3
PA1: U2.77 ((AD1)PA1), X25.1, X31.3
PA2: U2.76 ((AD2)PA2), X26.1, X32.3
PB0_SS: U2.19 ((SS/PCINT0)PB0), X12.6
PB1_SCK: U2.20 ((SCK/PCINT1)PB1), U4.P08 (SCK), X12.5, X18.3
PB2_MOSI: U2.21 ((MOSI/PCINT2)PB2), U4.P07 (SDI), X12.4, X18.4
PB3_MISO: U2.22 ((MISO/PCINT3)PB3), X12.3, X18.1
PC5: U2.58 ((A13)PC5), X20.4
PC6: U2.59 ((A14)PC6), X31.4
PC7: U2.60 ((A15)PC7), X24.1, X32.4
PD4: U2.47 ((ICP1)PD4), X13.14
PD5: U2.48 ((XCK1)PD5), X13.12
PD6: U2.49 ((T1)PD6), X13.10
PE2: U2.4 ((XCK0/AIN0)PE2), X13.20
PE3: U2.5 ((OC3A/AIN1)PE3), X34.5
PE6: U2.8 ((T3/INT6)PE6), X13.18
PE7: U2.9 ((CLKO/ICP3/INT7)PE7), X13.16
PF3: U2.94 ((ADC3)PF3), X40.4
PF4: U2.93 ((ADC4/TCK)PF4), X40.6
PF5: U2.92 ((ADC5/TMS)PF5), X40.8
PF6: U2.91 ((ADC6/TDO)PF6), X40.3
PG3: U2.28 ((TOSC2)PG3), X13.7
PG4: U2.29 ((TOSC1)PG4), X13.5
PG5: U2.1 ((OC0B)PG5), X5.1, X34.6
PH2: U2.14 (PH2(XCK2)), X13.8
PH7: U2.27 (PH7(T4)), X13.6
PJ2: U2.65 (PJ2(XCK3/PCINT11)), X13.9
PJ3: U2.66 (PJ3(PCINT12)), X13.11
PJ4: U2.67 (PJ4(PCINT13)), X13.15
PJ5: U2.68 (PJ5(PCINT14)), X13.17
PJ6: U2.69 (PJ6(PCINT15)), X13.19
PJ7: U2.79 (PJ7), X13.13
PK0: U2.89 (PK0(ADC8/PCINT16)), X40.7
PL3: U2.38 (PL3(OC5A)), X12.2, X32.5
PL4: U2.39 (PL4(OC5B)), X31.5
PL5: U2.40 (PL5(OC5C)), X20.5
RD+: R2.2, U1.29 (D+)
RD-: R1.2, U1.30 (D-)
RESET: C1.1, C10.2, D5.A, R46.1, S1.1, U2.30 (RESET), X18.5
RESET2: D4.A, R47.1, U1.24 (RESET(PC1/DW)), X17.5
RST-IO: C10.1, U10.14 (VOA)
RX0: R34.2, U2.2 ((RXD0/PCIN8)PE0), X39.3
RX0-I: U1.9 ((TXD1/INT3)PD3), U10.5 (VIC)
RX1: U2.45 ((RXD1/INT2)PD2), X39.5
RX2: U2.12 (PH0(RXD2)), X39.7
RX3: U2.63 (PJ0(RXD3/PCINT9)), X39.9
RXL: LED10.C, U1.10 ((INT5/AIN3)PD4)
SCK2: U1.15 ((SCLK/PCINT1)PB1), X17.3
SCL: R45.1, U2.43 ((SCL/INT0)PD0), X10.4
SDA: R44.1, U2.44 ((SDA/INT1)PD1), X10.3
THERM0: C59.1, D11.A, D13.C, R32.1, TP20.TP, U2.97 ((ADC0)PF0)
THERM1: C56.1, D14.A, D15.C, R37.1, TP21.TP, U2.96 ((ADC1)PF1)
THERM2: C64.1, D16.A, D17.C, R28.1, TP22.TP, U2.95 ((ADC2)PF2)
THERM3: C3.1, D18.A, D19.C, R39.1, TP23.TP, U2.90 ((ADC7/TDI)PF7), X40.5
TX0: U2.3 ((TXD0)PE1), U10.11 (VID), X39.4
TX0-I: U1.8 ((RXD1/AIN1/INT2)PD2), U10.6 (VOD)
TX1: U2.46 ((TXD1/INT3)PD3), X39.6
TX2: U2.13 (PH1(TXD2)), X39.8
TX3: U2.64 (PJ1(TXD3/PCINT10)), X39.10
TXL: LED9.C, U1.11 ((XCK/AIN4/PCINT12)PD5)
U1-PB0: U1.14 ((SS/PCINT0)PB0), X16.7
U1-PB4: U1.18 ((T1/PCINT4)PB4), X16.9
U1-PB5: U1.19 ((PCINT5)PB5), X16.12
U1-PB6: U1.20 ((PCINT6)PB6), X16.11
U1-PB7: U1.21 ((PCINT7/OC0A/OC1C)PB7), X16.14
U1-PC2: U1.5 ((AIN2/PCINT11)PC2), X16.5
U1-PC4: U1.26 ((PCINT10)PC4)
U1-PC5: U1.25 ((PCINT9/OC1B)PC5), X16.15
U1-PC6: U1.23 ((OC1A/PCINT8)PC6), X16.16
U1-PC7: U1.22 ((INT4/ICP1/CLK0)PC7), X16.13
U1-PD0: U1.6 ((OC0B/INT0)PD0), X16.10
U1-PD1: U1.7 ((AIN0/INT1)PD1), X16.8
U1-PD6: U1.12 ((RTS/AIN5/INT6)PD6), X16.6
USBVCC: C2.2, C5.1, C11.1, C14.1, C15.1, C19.1, D4.C, F1.1, R47.2, RN5.2 (1), RN5.3 (1), RN5.4 (1), U1.4 (VCC), U1.31 (UVCC), U1.32 (AVCC), U10.1 (VDD1A), U10.7 (VDD1B), X16.1, X16.2, X17.2
USHIELD: C63.1, R72.2, X2.P$1, X2.P$2, Z1.1, Z2.1
VCC: C7.1, C8.1, C9.1, C20.1, C21.2, C25.1, C30.1, C52.1, C53.1, C55.1, D5.C, L2.1, L3.P$2 (2), R13.2, R27.2, R29.2, R30.1, R31.2, R35.1, R36.2, R38.2, R44.2, R45.2, R46.2, R59.1, R60.1, R61.1, R62.1, R63.1, R65.2, R66.2, R67.2, R68.2, U2.10 (VCC), U2.31 (VCC1), U2.61 (VCC2), U2.80 (VCC3), U4.P06 (VDD), U10.10 (VDD2B), U10.16 (VDD2A), X1.2, X5.2, X10.1, X12.1, X13.1, X13.2, X18.2, X20.1, X21.3, X22.3, X23.3, X24.3, X25.3, X26.3, X31.1, X32.1, X34.1, X39.1, X40.1
VUCAP: C16.1, U1.27 (UCAP)
X-DIR: TP1.TP, U2.36 (PL1(ICP5)), U5.20 (DIR)
X-EN: R60.2, TP4.TP, U2.71 ((AD7)PA7), U5.5 (EN)
X-MIN: U2.25 ((OC1B/PCINT6)PB6), X23.1
X-MS1: U2.52 ((RD)PG1), U5.11 (MS1)
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

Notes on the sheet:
(SCK)
(MISO)
(MOSI)
pwm
(TX0)
(RX0)
USB boot En
int
csa
(SS)
Reference Designs ARE PROVIDED "AS IS" AND "WITH ALL FAULTS". We DISCLAIMS ALL OTHER WARRANTIES, EXPRESS OR IMPLIED, REGARDING PRODUCTS, INCLUDING BUT NOT LIMITED TO, ANY IMPLIED WARRANTIES OF
MERCHANTABILITY OR FITNESS FOR A PARTICULAR PURPOSE.
or instructions marked "reserved" or "undefined." We reserve these for future definition and shall have no responsibility whatsoever for conflicts or incompatibilities arising from future changes to them. The product information on the
Web Site or Materials is subject to change without notice. Do not finalize a design with this information.
A10
A11
A12
A13
A14
A15
Motor Extensions
SPI Extension
PWM Extension
RAMBo 1.3a
Atmega 32u2 USB
I2C Expansion
Atmega2560 Programmer
Power In
Power Supply
Stepper Motor Drivers
Digipot
Thermistors
Mosfets
Aux Power Out
Design by Johnny Russell - UltiMachine
Based on work by the Arduino Team and the RepRap project.
(R)epRap (A)rduino-(M)ega-compatible (M)other (Bo)ard
Serial Extension
Endstops
Atmega 2560

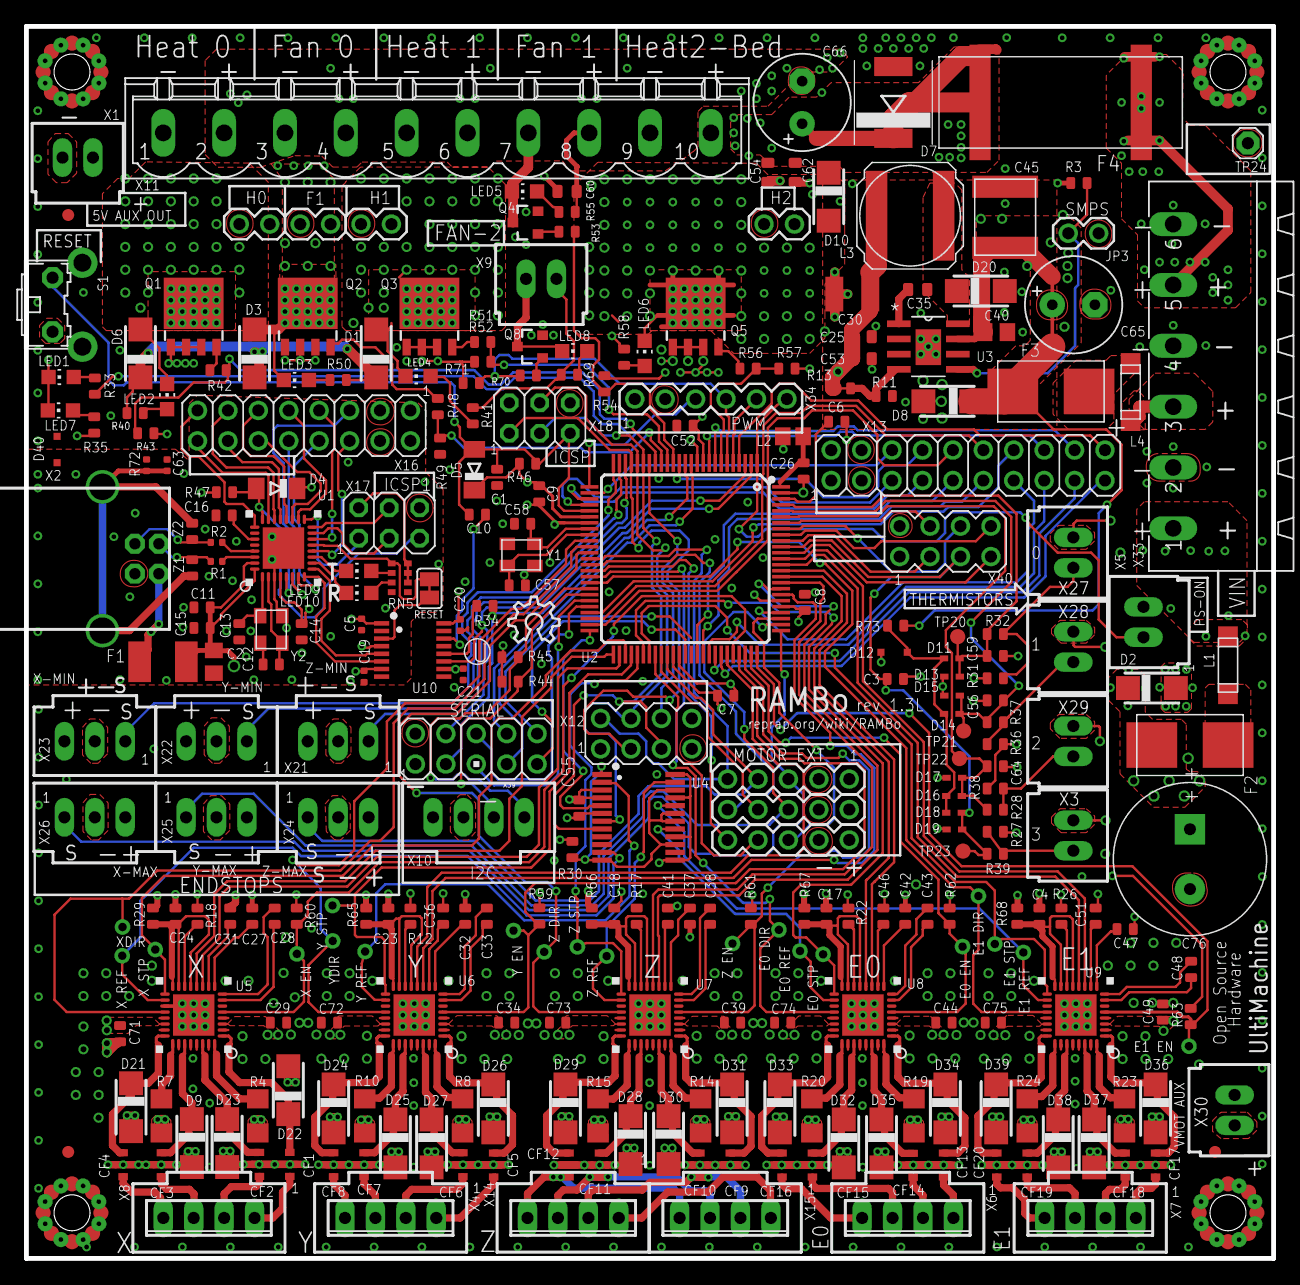
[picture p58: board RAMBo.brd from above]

Board: 4 copper layers, 104.1 x 102.9 mm, 309 parts (0 on the bottom side), 252 nets.

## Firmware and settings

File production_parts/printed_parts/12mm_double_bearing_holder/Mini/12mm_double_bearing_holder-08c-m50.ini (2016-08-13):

[profile]
layer_height = .39
wall_thickness = 1.0
retraction_enable = True
solid_layer_thickness = .78
fill_density = 35
perimeter_before_infill = True
nozzle_size = 0.5
print_speed = 60
print_temperature = 250
print_temperature2 = 0
print_temperature3 = 0
print_temperature4 = 0
print_temperature5 = 0
print_bed_temperature = 110
support = None
platform_adhesion = None
support_dual_extrusion = Both
wipe_tower = False
wipe_tower_volume = 15
ooze_shield = False
filament_diameter = 2.85
filament_diameter2 = 0
filament_diameter3 = 0
filament_diameter4 = 0
filament_diameter5 = 0
filament_flow = 98.0
retraction_speed = 10
retraction_amount = 1.5
retraction_dual_amount = 16.5
retraction_min_travel = 1.5
retraction_combing = True
retraction_minimal_extrusion = 0.02
retraction_hop = 0.1
bottom_thickness = .35
layer0_width_factor = 187
object_sink = 0.0
overlap_dual = 0.15
travel_speed = 175
bottom_layer_speed = 25
infill_speed = 60
solidarea_speed = 60
inset0_speed = 50
insetx_speed = 50
cool_min_layer_time = 15
fan_enabled = True
skirt_line_count = 1
skirt_gap = 3.0
skirt_minimal_length = 250.0
fan_full_height = 5
fan_speed = 40
fan_speed_max = 60
cool_min_feedrate = 10
cool_head_lift = False
solid_top = True
solid_bottom = True
fill_overlap = 15
support_type = Lines
support_angle = 45
support_fill_rate = 30
support_xy_distance = 0.7
support_z_distance = 0.05
spiralize = False
simple_mode = False
brim_line_count = 10
raft_margin = 5.0
raft_line_spacing = 3.0
raft_base_thickness = 0.3
raft_base_linewidth = 1.0
raft_interface_thickness = 0.27
raft_interface_linewidth = 0.4
raft_airgap_all = 0.0
raft_airgap = 0.5
raft_surface_layers = 2
raft_surface_thickness = 0.27
raft_surface_linewidth = 0.4
fix_horrible_union_all_type_a = True
fix_horrible_union_all_type_b = False
fix_horrible_use_open_bits = False
fix_horrible_extensive_stitching = False
plugin_config = 
object_center_x = -1
object_center_y = -1
simplemodesettings = 
simplemodeprofile = Standard
simplemodematerial = PLA
simplemodematerialtype = Beginner

[alterations]
start.gcode = ;Basic settings: Layer height: {layer_height} Walls: {wall_thickness} Fill: {fill_density}
	;Print time: {print_time}
	;Filament used: {filament_amount}m {filament_weight}g
	;Filament cost: {filament_cost}
	;M190 S{print_bed_temperature} ;Uncomment to add your own bed temperature line
	;M109 S{print_temperature} ;Uncomment to add your own temperature line
	G21                          ; metric values
	G90                          ; absolute positioning
	M82                          ; set extruder to absolute mode
	M107                         ; start with the fan off
	G92 E0                       ; set extruder position to 0
	M140 S{print_bed_temperature}; get bed heating up
	G28                          ; home all
	M109 S150                    ; set to cleaning temp and wait
	G1 Z150 E-30 F75             ; suck up XXmm of filament
	M109 S170                    ; heat up rest of way
	G1 X45 Y174 F11520           ; move behind scraper
	G1 Z0  F1200                 ; CRITICAL: set Z to height of top of scraper
	G1 X45 Y174 Z-.5 F4000       ; wiping ; plunge into wipe pad
	G1 X55 Y172 Z-.5 F4000       ; wiping
	G1 X45 Y174 Z0 F4000         ; wiping
	G1 X55 Y172 F4000            ; wiping
	G1 X45 Y174 F4000            ; wiping
	G1 X55 Y172 F4000            ; wiping
	G1 X45 Y174 F4000            ; wiping
	G1 X55 Y172 F4000            ; wiping
	G1 X60 Y174 F4000            ; wiping
	G1 X80 Y172 F4000            ; wiping
	G1 X60 Y174 F4000            ; wiping
	G1 X80 Y172 F4000            ; wiping
	G1 X60 Y174 F4000            ; wiping
	G1 X90 Y172 F4000            ; wiping
	G1 X80 Y174 F4000            ; wiping
	G1 X100 Y172 F4000           ; wiping
	G1 X80 Y174 F4000            ; wiping
	G1 X100 Y172 F4000           ; wiping
	G1 X80 Y174 F4000            ; wiping
	G1 X100 Y172 F4000           ; wiping
	G1 X110 Y174 F4000           ; wiping
	G1 X100 Y172 F4000           ; wiping
	G1 X110 Y174 F4000           ; wiping
	G1 X100 Y172 F4000           ; wiping
	G1 X110 Y174 F4000           ; wiping
	G1 X115 Y172 Z-0.5 F1000     ; wipe slower and bury noz in cleanish area
	G1 Z10                       ; raise z
	G28 X0 Y0                    ; home x and y
	M109 S170                    ; set to probing temp
	M204 S300                    ; set accel for probing
	G29                          ; Probe
	M204 S2000                   ; set accel back to normal
	G1 X5 Y15 Z10 F5000          ; get out the way
	M400                         ; clear buffer
	G4 S1                        ; pause
	M109 S{print_temperature}    ; set extruder temp and wait
	G4 S25                       ; wait for bed to temp up
	G1 Z2 E0 F75                 ; extrude filament back into nozzle
	M140 S{print_bed_temperature}; get bed temping up during first layer
end.gcode = M400
	M104 S0                         ; Hotend off
	M140 S0                         ; heated bed heater off (if you have it)
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

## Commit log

2016-08-13 all but large files?
    [10mmx500mm_rod_v0.1.fcstd, 12mm_double_bearing_holder_v0.7.fcstd, 12mm_double_bearing_holder_v0.7.stl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]
2016-08-14 new directory for assembly instructions
2016-08-14 better file path structure
    [LulzBot_keychain.stl, OSHW_logo.stl, XY_resonance_1.0mm_walls.stl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]

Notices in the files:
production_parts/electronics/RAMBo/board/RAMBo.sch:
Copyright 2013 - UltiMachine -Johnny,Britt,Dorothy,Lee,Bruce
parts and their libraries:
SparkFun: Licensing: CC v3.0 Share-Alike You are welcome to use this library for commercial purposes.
